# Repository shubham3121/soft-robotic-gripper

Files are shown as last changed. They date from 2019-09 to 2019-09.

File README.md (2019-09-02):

# soft-robotic-gripper

This was my under-graduate final year research project. This project captures the developement of a soft robotic gripper that exhibits the grasping and release action similar to a human hand. The use of NiTi coils as actuators, instead of servo motors, for producing the grasp and release motion, differentiates this robotic gripper from existing ones. This repository consits of:
- source code files for the micro-controller
- Related cad models and gcode files
- Detailed report on the robotic gripper
- A copy of the paper that was submitted to IEEE Transactions on Robotics (RAS Society)
- Link to video of the prototype: https://youtu.be/JxMexBUdsPk

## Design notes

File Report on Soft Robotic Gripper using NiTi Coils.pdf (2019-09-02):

### A Project on

## Soft Robotic Gripper Using NiTi Coils

### Submitted for fulfilment of award of

### Bachelor of Technology

In

### Electrical and Electronics

By

### Raghvendra Singh Shubham Gupta Utkarsh Rastogi

### Under the Guidance of

### Vikash Kumar Rahul Dixit

### AJAY KUMAR GARG ENGINEERING COLLEGE, GHAZIABAD

### YEAR: 2015-2016

AJAY KUMAR GARG ENGINEERING COLLEGE,

### GHAZIABAD

# CERTIFICATE

### This is to certify that Project Report entitled "SOFT ROBOTIC GRIPPER

### USING NiTi COILS” which is submitted by Raghvendra Singh, Shubham

### Gupta and Utkarsh Rastogi in the partial fulfillment of requirement for the

### award of degree of Bachelor of Technology (Electrical and Electronic

### Engineering) submitted to A.P.J Abdul Kalam Technical University, Lucknow

### is a record of students' own work carried out under my supervision. The

### matter in this report has not been submitted to any University or Institution

for award of any degree.

Supervisors:
Vikash Kumar
Rahul Dixit

HOD:
Prof. Ashiv Shah
TIFAC CORE

Date: 29th April, 2016.

ACKNOWLEDGEMENT

We take this opportunity to express our deep sense of gratitude and regard to Mr. Vikash Kumar

(TIFAC CORE Deptt.) and Mr. Rahul Dixit (TIFAC CORE Deptt.), Ajay Kumar Garg

Engineering College, Ghaziabad for his continuous encouragement and able guidance, we needed

to complete this project.

We would pay sincere gratitude to the Head of the Deptt. (TIFAC CORE) Prof. Ashiv Shah for his

precious and enlightening words of wisdom which motivated us throughout our project work.

We are also grateful to Mr. Ashish Gupta and Mr. Harikesh Bahadur Singh for their continuous

support and valuable suggestions.

DECLARATION

### We hereby declare that this submission is our own work and that, to the best

### of out knowledge and belief, it contains no material previously published or

### written by another person, nor material which to a substantial extent has been

### accepted for the award of any other degree or diploma by the university or

### other institute of higher learning, except where due acknowledgement has

been made in the text.

### Signature:

1.

### Name: Shubham Gupta

### Roll No. : 1202721090

2.

### Name: Raghvendra Singh

### Roll No. : 1202721065

3.

### Name: Utkarsh Rastogi

### Roll No. : 1202731109

Chapter 1.

Chapters | | PageNo.
Chapter I:`` Introduction | 1-5
1.1 | Robot End Effectors | 1
1.2 | Biologically Inspired Engineering | 2
| 1.2.1 Bio-inspired Robotics | 2
| 1.2.1.1 Soft Robotics | 3
1.3 | Mechanism of Gripping | 3
| 1.3.1 Shape of the Gripping Surface | 3
| 1.3.2 Force Required to Grip the Object | 3
1.4 | Examples of End Effectors | 4
Chapter II: Literature Review, Requirement Analysis & Feasibility Study | 6-19
2.1 | Literature Review | 6
| 2.1.1 NiTi Coil Actuators as Micro Artificial Muscle Fibers | 7
| 2.1.2 Modelling of NiTi Coil Actuators | 7
| 2.1.3 Fabrication & Characteristics of NiTi Coils | 10
2.2 | Requirement Analysis | 13
| 2.2.1 Initial Proposed Wire & Spring Specifications | 13
| 2.2.1.1 Cost Associated | 14
2.2.2 Designing of Coil Actuators using Standard NiTi Springs 14
| 2.2.2.1 Stretch Ratio | 14
| 2.2.2.2 New Spring Specifications | 15
2.3 | Feasibility Analysis | 16
| 2.3.1 Operational Feasibility | 16
| 2.3.2 Electrical Guidelines | 18
| 2.3.3 Cycle Time | 18
Chapter III: System Analysis, Modelling & Design | 20-29
3.1 | System Analysis | 20
3.2 | Modelling of the Spring Actuators | 21
3.3 | Modelling of the Fingers of the Gripper | 22
| 3.3.1 Designing of the Finger Link | 23
| 3.3.2 Fabrication of the Link | 24
| 3.3.3 Construction of the Finger of the Gripper | 25
| 3.3.4 Designing & Modelling Of Gripper Base | 27
3.4 | Assembling of the Three Finger Gripper | 28
Chapter IV: Hardware & Software Specifications | 30-42
4.1 | Hardware Specifications | 30
| 4.1.1 BC368 NPN General Purpose Amplifier | 30
| 4.1.2 Tiva™ TM4C123GH6PM Microcontroller | 32
| 4.1.2.1 TM4C123GH6PM Microcontroller Overview | 33
| 4.1.2.2 TM4C123GH6PM Microcontroller Pin Structure | 33
| 4.1.2.3 Tiva Launchpad based on TM4C123GH6PM | 35
| 4.1.3 LM2596 DC-DC Step Down Buck Converter | 37

TABLE OF CONTENTS

4.2 | Software Specifications | 38
4.2.1 Code for the Microcontroller | 39
4.3 | Control Circuit for the Gripper | 41
Chapter V: Working of Project | 42-45
5.1 | Analogy between the Human Hand & the Robotic Gripper | 43
5.1.1 Power Grip | 43
5.1.2 Precision Grip | 43
5.2 | Implementation of the Robotic Gripper | 44
Chapter VI: Results & Discussion | 46-47
6.1 | Advantages of Developed System | 46
6.2 | Limitations | 46
Chapter VII: Conclusion & Future Scope | 48
7.1 | Conclusion | 48
7.2 | Future Scope | 48
References

LIST OF FIGURES

Figure 1.1 | Examples of End Effector | 5
Figure 2.1 | Image of a muscle fiber of 400µm diameter and length of 0.5m | 6
Figure 2.2 | Five representational states of a NiTi coil spring actuator in Austenite and Martensite phase with and without load . | 8
Figure 2.3 | Diagram shows a simple manufacturing system that enables the fabrication of long strand coiled springs of NiTi muscle fiber | 10
Figure 2.4. | Experimental results of NiTi coil spring ... | 12
Figure 2.5 | Example of Stretch Ratio | 15
Figure 2.6 | Various basic structures and the percentage of movement of NiTi wire/coils | 17
Figure 3.1 | Bones of the left hand (Volar Surface) | 20
Figure 3.2 | Front, Top and left view of the finger link | 23
Figure 3.3 | Ultimaker2 and the spool of used as the printing filament | 25
Figure 3.4 | Representation of the various components in the link model | 26
Figure 3.5 | Front, Left and Isometric view of the assembly of finger links | 26
Figure 3.6 | Top, Left and Front view of the model of the gripper | 28
Figure 3.7 | Snapshots of the three fingers of the gripper and a completely assembled gripper | 29
Figure 4.1 | Pin configuration of BC368 NPN General Purpose Amplifier | 31
Figure 4.2 | Table showing the features of TM4C123GH6PM Microcontroller | 33
Figure 4.3 | I/O port pins for the TM4C123GH6PM Microcontroller | 34
Figure 4.4 | Tiva LaunchPad based on the TM4C123GH6PM | 35
Figure 4.5 | Switch and LED interfaces on the Tiva LaunchPad Evaluation Board | 36
Figure 4.6 | Interface connectors on the Tiva TM4C123 LaunchPad Evaluation Board | 36
Figure 4.7 | LM2596 DC-DC Step down Buck Converter and its circuit diagram | 37
Figure 4.8 | Control circuit for the robotic gripper | 41
Figure 5.1 | Control circuit during grasp action and release action of the gripper | 45
Figure 6.1 | Gripper during gripping of an object | 46

ABSTRACT

Robotics is basically based on the fundamental assumption that robots are chain of rigid links but ‘Soft Robotics’ which is the use of soft materials in robotics that can vary their stiffness and thus can undergo high deformations during interactions that overcomes robot’s basic assumptions and thus removes many bottlenecks of rigid links in robots. They can have mechanisms for varying the material characteristics such as stiffness, elasticity and surface properties, etc. for generating motion through muscles and for facilitating sensing in skins through embedded mechanoreceptors. Soft materials may enable us to automate tasks that are beyond capacities of current robotics technology and thus the complex, precise control architecture can be simplified using highly compliant materials with variable stiffness. Soft Robots has the expected capability to interact more
easily and effectively with the real world environment. | Soft Robotics has the potential to
produce a new generation of better robots.
This report presents the development and analysis of a soft robotic platform that exhibits the grasping and release action of a human hand. The design of the gripper is basically based on a human hand except for the fact that all the joint to joint distances in a finger are equal. Each finger is composed of four sub-components and three fingers are joint together to a base to form the hand. Nickel titanium (NiTi) coils are used as the actuating medium and are placed across the joints of the finger. The finger sub-components are made of PLA using a 3D printer. The actuation of the nickel titanium coils is controlled through a constant current supply, controlled through a switching circuit and a microcontroller. This approach allows for a simple, low cost, energy efficient gripper. The report further analysis and discusses the potential use and application of this platform.

Index Terms—Robotic gripper, nickel titanium (NiTi) coil actuators, PLA, soft robotics, shape memory alloys (SMA) actuation, microcontroller, 3D printer.

Chapter 1.
INTRODUCTION
1.1 | Robot End Effectors
| In robotics, an end effector is the device at the end of a robotic arm, designed to
interact with the environment. The exact nature of this device depends on the application of the robot. In the strict definition, which originates from serial robotic manipulators, the end effector means the last link (or end) of the robot. At this endpoint the tools are attached. In a wider sense, an end effector can be seen as the part of a robot that interacts with the work environment. This does not refer to the wheels of a mobile robot or the feet of a humanoid robot which are also not end effectors—they are part of the robot's mobility.
| End effectors may consist of a gripper or a tool. When referring to robotic prehension
there are four general categories of robot grippers, these are: [1]
a) Impactive – jaws or claws which physically grasp by direct impact upon the object.
b) Ingressive – pins, needles or hackles which physically penetrate the surface of the
| object (used in textile, carbon and glass fibre handling).
c) Astrictive – suction forces applied to the objects surface (whether by vacuum,
| magneto or electro adhesion).
d) Contigutive – requiring direct contact for adhesion to take place (such as glue,
| surface tension or freezing). They are based on different physical effects used to guarantee a stable grasping

between a gripper and the object to be grasped.[2] Industrial grippers can be mechanical, the most diffused in industry, but also based on suction or on the magnetic force. Vacuum cups and electromagnets dominate the automotive field and in particular metal sheet handling. Bernoulli grippers exploit the airflow between the gripper and the part that causes a lifting force which brings the gripper and part close each other (i.e. the Bernoulli's principle). Bernoulli grippers are a type of contactless grippers, namely the object remains confined in the force field generated by the gripper without coming into direct contact with it. Bernoulli grippers have been adopted in photovoltaic cell handling, silicon wafer handling, and also in the textile and leather industries. Other principles are less used at the macro scale (part size >5mm), but in the last ten years they demonstrated interesting applications in micro handling. Some of them are ready of spreading out their original field. The other adopted principles are: Electrostatic grippers and van der Waals grippers based on electrostatic charges (i.e. van der Waals' force), capillary grippers and cryogenic grippers, based on liquid medium, and ultrasonic grippers and laser grippers, two contactless grasping principles. Electrostatic grippers are based on charge difference between the gripper and the part (i.e. electrostatic force) often activated by the gripper itself, while van der Waals grippers are based on the low force (still electrostatic) due to the atomic attraction between the molecules of the gripper and those of the object.
| Capillary grippers use the surface tension of a liquid meniscus between the gripper
and the part to center, align and grasp the part, cryogenic grippers freeze a small amount of liquid and the resulting ice guarantees the necessary force to lift and handle the object (this principle is used also in food handling and in textile grasping). Even more complex are ultrasonic based grippers, where pressure standing waves are used to lift up a part and trap it at a certain level (example of levitation are both at the micro level, in screw and gasket handling, and at the macro scale, in solar cell or silicon wafer handling), and laser source that produces a pressure able to trap and move micro parts in a liquid medium (mainly cells). The laser gripper are known also as laser tweezers.
A particular category of friction/jaw gripper are the needle grippers: they are called intrusive grippers and exploits both friction and form closure as standard mechanical grippers. The most known grippers can be of two, three or even five fingers. The end effectors that can be used as tools serve various purposes, such as spot welding in an assembly, spray painting where uniformity of painting is necessary, and for other purposes where the working conditions are dangerous for human beings. Surgical robots have end effectors that are specifically manufactured for the purpose.

1.2 Biologically Inspired Engineering

[3] Biologically inspired engineering is a new scientific discipline that applies biological principles to develop new engineering solutions for medicine, industry, the environment, and many other fields that have previously not been touched by the biology revolution. The emergence of this new discipline is the culmination of the unification of the life sciences with engineering and the physical sciences, and it is leading to an ever deeper understanding of how life works. Biologically inspired engineering involves deep exploration into the way that living cells, tissues, and organisms build, control, manufacture, recycle, and adapt to their environment. Bioinspired engineers leverage this knowledge to innovate new technologies and translate them into products that meet real world challenges.
| Biologically inspired engineering is an interdisciplinary field encompassing many
specialty areas in biology (molecular cell biology, genetic engineering, developmental biology, organismal biology, clinical medicine), engineering (biomedical engineering, chemical engineering, mechanical engineering, electrical engineering, robotics), and the physical sciences (chemistry, physics, materials science, and nanotechnology). Integrated research programs in this area span many of these disciplines and include biomimicry, as well as analysis of the way that living systems form and function using self-assembling nanomaterials, complex dynamic networks, nonlinear dynamical control, self-organizing behaviour, evolution, and natural selection.

1.2.1 Bio-inspired Robotics

| Bio-inspired robotic locomotion is a fairly new sub-category of bio-inspired
design. It is about learning concepts from nature and applying them to the design of real world engineered systems. More specifically, this field is about making robots that are inspired by biological systems. Biomimicry and bio-inspired design are sometimes confused. Biomimicry is copying the nature while bio-inspired design is learning from nature and making a mechanism that is simpler and more effective than the system observed in nature. Biomimicry has led to the development of a different branch of robotics called soft robotics. The biological systems have been optimized for specific tasks according to their habitat. However, they are multi-functional and are not designed for only one specific functionality.
| Bio-inspired robotics is about studying biological systems, and look for the
mechanisms that may solve a problem in the engineering field. The designer should then try to simplify and enhance that mechanism for the specific task of interest. Bio-inspired roboticists are usually interested in biosensors (e.g. eye), bio actuators (e.g. muscle), or biomaterials (e.g. spider silk). Most of the robots have some type of locomotion system. Thus, in this article different modes of animal locomotion and few examples of the corresponding bio-inspired robots are introduced.

1.2.1.1 Soft Robotics

Soft robotics (https://en.wikipedia.org/w/index.php?title=Soft_robotics&action=edit&redlink=1) [4] is a new field in robotics and the idea is to make all of the components in the robot soft and flexible in order to move in very limited spaces and change gaits fairly easily. This field is inspired by animals such as octopus (https://en.wikipedia.org/wiki/Octopus) or starfish. (https://en.wikipedia.org/wiki/Starfish) One of the first multigait soft robots is developed at Harvard University and is inspired by
starfish. | [5] | Soft robotics is not just a new direction of technological development, but a
novel approach to robotics, unhinging its fundamentals, with the potential to produce a new generation of robots, in the support of humans in our natural environments.
1.3 | Mechanism of Gripping
| A common form of robotic grasping is force closure. [6] Generally, the gripping
mechanism is done by the grippers or mechanical fingers. Generally only two finger grippers are used for industrial robots as they tend to be built for specific tasks and can therefore be less complex.
The fingers are also replaceable whether or not the gripper itself is replaced. There are two mechanisms of gripping the object in between the fingers (for the sake of simplicity, the following explanations consider only two finger grippers).

1.3.1 Shape of the gripping surface

| The shape of the gripping surface of the fingers can be chosen according to the
shape of the objects that are to be manipulated. For example, if a robot is designed to lift a round object, the gripper surface shape can be a concave impression of it to make the grip efficient, or for a square shape the surface can be a plane.

1.3.2 Force required to grip the object

| Though there are numerous forces acting over the body that has been lifted by the
robotic arm, the main force acting there is the frictional force. The gripping surface can be made of a soft material with high coefficient of friction so that the surface of the object is not damaged. The robotic gripper must withstand not only the weight of the object but also acceleration and the motion that is caused due to frequent movement of the object. To find out the force required to grip the object, the following formula is used:

F = µWn
| Where: F is the force required to grip the object, µ is the coefficient of friction, n is the number of fingers in the gripper and W is the weight of the object.

But the above equation is incomplete. The direction of the movement also plays an important role over the gripping of the object. For example, when the body is moved upwards, against the gravitational force, the force required will be more than towards the gravitational force. Hence, another term is introduced and the formula becomes:

F = µWng

Here, the value of g should not be taken as the acceleration due to gravity. In fact, here g stands for multiplication factor. The value of g ranges from 1 to 3. When the body is moved in the horizontal direction then the value is taken to be 2, when moved against the gravitational force then 3 and along the gravitational force, i.e., downwards, 1.

1.4 | Examples of End effectors
| The end effector of an assembly line robot would typically be a welding head, or a
paint spray gun. A surgical robot's end effector could be a scalpel or others tools used in surgery. Other possible end effectors are machine tools, like a drill or milling cutters. The end effector on the space shuttle’s robotic arm uses a pattern of wires which close like the aperture of a camera around a handle or other grasping point.
(a.) | (b.)
(c.) | (d.)

(e)

Fig. 1.1 (a.) An example of a basic force-closure end effector. (b.) A spot welding end effector. (c.) A repair and observation end effector in use in space (Canadarm2). (d.) A highly sophisticated attempt at reproducing the human-hand force-closure end effector. (e.) Laser Welding end effector.

Chapter 2.
LITERATURE REVIEW, REQUIREMENT ANALYSIS & FEASIBILITY

2.1 Literature Review

[7] Soft robotics is an emerging field that introduces a number of new challenges to roboticists. Soft robots will consist of a flexible body, possess an ability to deform their shape as dictated by various environments, and exhibit superb robustness upon impacts. One of the most challenging elements of such a robot is the soft actuator. Most conventional actuators contain rigid components that limit morphing ability, however a soft actuator can deform along with the surrounding structure.
| One of these soft actuators is Nickel Titanium (NiTi) a Shape Memory Alloy (SMA),
since its unique martensite transformation makes it inherently flexible. It is also well known for its high energy density, despite its poor efficiency. NiTi has great advantages especially in a small scale where other types of actuators are not available or exhibit poor energy density. The NiTi crystal lattice transforms from the martensite state to the austenite state and produces up to 4% length change as it is heated through the transition temperature range. Some applications require more operating strain to satisfy the dimensional constraints. In order to create larger stroke lengths out of a small lattice structure alteration, NiTi can be restructured into coil springs.

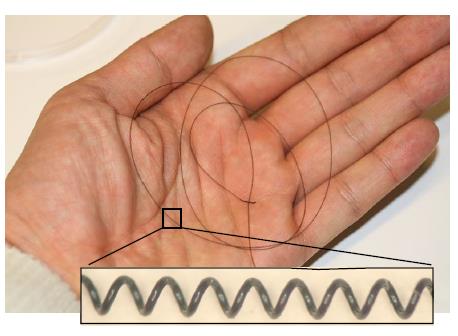
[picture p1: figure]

Fig. 2.1 Fabricated muscle fiber is 400µm in diameter and 0.5m

Chang et al. [8], discuss the numerous models for NiTi that has been proposed since the early 1990s. Most of them are thermodynamic models of NiTi wires, tubes, and sheets. Some papers discuss NiTi springs [9], [10], [11], [12], [13], but the models used in these papers are not complete. The paper [7], presents a more complete model that can be used as a design guideline for NiTi spring actuators.

NiTi coil springs are created from straight wire wound into a coil shape and annealed at a high temperature to reset the ‘memorized’ shape. The annealing temperature used in the reshaping process affects mechanical properties of NiTi and actuation performance. The results from experiments to show the variation in properties due to the variation in annealing temperature have also been presented. These experiments include detwinning force and loaded displacement measurements. After weightlifting test, springs shows permanent deformation, which is also function of the annealing temperature.

2.1.1 NiTi Coil Actuators as Micro Artificial Muscle Fibers

NiTi is one of the well-known SMA materials that generate mechanical work by phase change. Despite its low efficiency, it has a high energy density, which gives the ability to develop relatively small scale actuators compared to other types of actuators mentioned in Section I. In a solid state phase transformation, the crystal structure of the NiTi compound transforms from martensite to austenite states with up to 7% strain change [14]. For larger displacements, coiled spring NiTi wires can be used.
Various NiTi models suggested from the 1990s are discussed in [15]. These are mostly thermodynamic models of various forms of NiTi such as wires, tubes, and sheets. Coiled spring NiTi models were discussed in [9], and [10]–[12]. These models, however, are relatively incomplete. The existing models focus on the mechanical coiled spring equations using different shear moduli for the martensite and austenite phases, overlooking the change in the free length of the spring due to the phase transition.
A more appropriate model, which is useful for a design of coiled spring NiTi is proposed in Section 2.1.2. This model combines the mechanical and thermodynamic aspects of NiTi coil actuators to describe the overall martensite deformation and the geometrical spring effect together. We use this model as a guideline for actuator design for the Meshworm robot.
There are two major steps to fabricate NiTi coil springs. First, a NiTi wire is wound around a straight core, and then the coiled NiTi wire is annealed at a certain high temperature in order to reset the memorized shape as a spring. During the annealing process, mechanical properties and the actuation performance of NiTi springs are determined by the annealing temperature. In Chapter 2.1.2, the manufacturing process is detailed and experimental data between deflection and force under various annealing temperatures are presented.

2.1.2 Modelling of NiTi Coil Actuators

Even though NiTi spring actuators are widely used [9], [10]–[12], complete design models have not been developed yet. Recent works utilize the mechanical coiled spring equation with two shear moduli, GMand GA which are the martensite and austenite phases, respectively. However, none of these models consider the free length change of the NiTi spring due to phase change. The free length of 100% austenite phase xAo is shorter than the free length of 100% martensite xMo.
There are two major physical phenomena in NiTi coil spring deformation. One is the free length change due to the phase transformation explained earlier, and the other is the spring constant difference between the martensite and austenite states. The spring constant in the austenite phase is around 2–3 times greater than in the martensite phase [15].

[16] Fig. 2.2 shows five typical states of a NiTi coil spring during actuation. When the NiTi coil is heated up above the phase transition temperature, it becomes austenite and fully contracts as in Fig. 2.2(a). If a load F is applied in this state, the spring will have a displacement δH as shown in Fig. 2.2(b). When the temperature is below the transition temperature, it becomes martensite and the crystal structure of NiTi twins [17] without an observable overall shape change [see Fig. 2.2(c)]. If a load is applied below the transition temperature, the crystal structure is detwinned [17]. Fig. 2.2(e) shows the detwinned martensite with a load F, and Fig. 2.2(d) shows the detwinned martensite in free length after the detwinning load is removed. The free length difference between austenite and detwinned martensite is δM. The displacement δL
is the length difference between loaded martensite and unloaded martensite under fully detwinned status.
In general, the NiTi spring actuation cycle starts in the martensite phase with an external load F. And then, the spring is activated by heating it up to transition temperature, which results in a spring length contraction under the load. The displacement created in this transformation is called effective displacement,δeffective and calculated as follows:
δeffective = δM + δL − δH | (1)

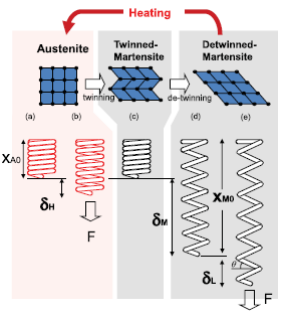
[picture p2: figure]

Fig. 2.2. Five representational states of a NiTi coil spring actuator: (a) full austenite without load (b) full austenite with load, (c) twinned martensite without load, (d) fully detwinned martensite without load, and (e) fully detwinned martensite with load.

Here, each δi value, where i ∈ {H, L, M}, corresponds to the displacement of the coil. Using the general coiled spring deflection equation, δi
is a function of an external load F, overall spring diameter D, NiTi wire diameter d, number of active coils in the spring n, and the shear modulus of the spring after annealing G

δi =

8FD

3n
Gd⁴

(2)

The shear strain γ of the spring is

γ =

τ
G

(3)

and the shear stress τ is

τ =

8FDҡ
πd³

(4)

where ҡ is a stress correction factor. From Wahl’s formula [18],

ҡ =

4C−1
4C−4

+

0.615
C
. | (5)

Here C is the spring index, defined as follows:

C =

D
d
. | (6)

Using this analysis, the difference of the free length between the austenite and martensite phases δM can be calculated from (2) through (4) as

δM =

πγD

2n

dҡ

. | (7)

Therefore, for a given F, the effective displacement from (1) is given as follows:

δeffective =

πγD

2n

dҡ

+

8FDeff

3 n
GMd⁴ −

8FD

3n
GAd⁴
. | (8)

There is a significant coil diameter D change when the coil spring is elongated under martensite phase with a load F. Therefore, to calculate the displacement properly in this situation, an effective spring diameter Deff is used

Deff = D cos θ

where θ is the angle between the spring wire and the horizontal plane.

2.1.3 Fabrication and Characterization of NiTi Coil Actuators

[16] The fabrication process of micro-NiTi coil muscle fibers is depicted schematically in Fig. 2.3. One end of a 200-μm diameter core wire and a 100-μm diameter NiTi wire [Dynalloy Flexinol (R)] are clamped at a drill press. Constant tension is applied to the core wire by attaching a weight on the free end. A metal tube and a bar attached to the tube make up the coil guide, which is essential for closely packing the NiTi coil on the core. The friction of the metal tube on the core acts against the tension from the coiled NiTi and keeps the core wire vertical.

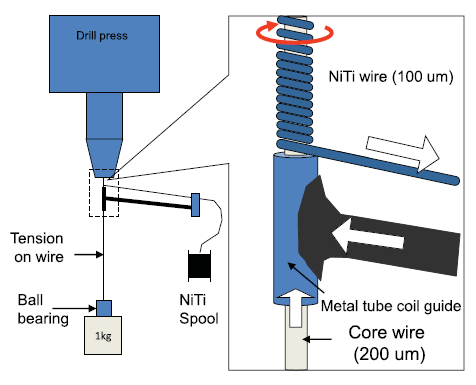
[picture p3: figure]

Fig. 2.3. Simple manufacturing system enables the fabrication of long strand coiled springs of NiTi muscle fiber. The core wire is under tension and a NiTi wire is wound around the core. The guidance tube is slightly larger than the core wire. The tension of the NiTi wire is maintained by friction between NiTi and the long bar.

After winding the NiTi wire to a given length, the ends of the coil are clamped to the core wire and annealed in an oven under a controlled temperature. The annealing temperature determines various parameters of the resulting spring actuator. Two noticeable trends are identified that vary with the annealing temperature: 1) increasing the annealing temperature decreases the detwinning force, and 2) large annealing temperatures cause the resulting springs to lose their ability to return to their original dimensions after loading. Detwinning is a passive process that returns the actuated NiTi coils in the twinned martensite state back to the fully detwinned martensite state through martensite transformation. This requires external work, such that a certain amount of tensile force pulls the coils to extend them, transforming their state in the process. This force is strongly dependant on the annealing temperature, and is a mechanical characteristic of the actuators. When used in an antagonistic configuration, such that the actuation of one coil detwins the other, this characteristic force requirement affects the full cycle work efficiency of the actuators.
We experimentally investigated the dependence of the detwinning force on the annealing temperature. 25-mm-long NiTi coil springs are annealed at nine different temperatures ranging from 300 ◦C to 540 ◦C in 30 ◦C increments. Weights are hanged on the coils to apply varying external forces. Weight application and removal were carried out slowly to reduce dynamic effects and the spring effect. The final elongated length was measured under no load, after the weights were removed.
Fig. 2.4(a) depicts the results. In these curves, detwinning is indicated as a plateau, similar to a plastic deformation behaviour in stress–strain curves. The value at which this plateau occurs is the detwinning force. This force clearly decreases with the increasing annealing temperature as a general trend. After detwinning, the coils yield a larger stiffness, indicated by a sharp gradient in the curve after the plateau. This stiffness change occurs at larger deflections as the annealing temperature is increased. We used an annealing period of 20 min for these experiments. We found no change in actuator characteristics above this value.

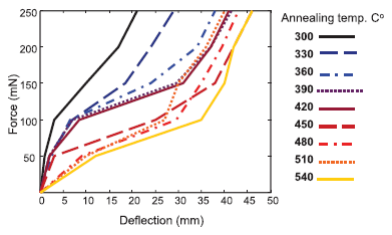
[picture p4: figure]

(a)

(b)

(c)

Fig. 2.4. Experimental results of NiTi coil spring. (a) Deflection of springs annealed at various temperatures under load. (b) Permanent plastic deformation of NiTi coil springs annealed at various temperatures, after lifting a 35-g weight. (c) Experimental NiTi coil spring deflection data are compared to the theoretical model predictions: Average errors in Martensite and Austenite phases’ are−22% and 12.4%, respectively.

The second effect of the annealing temperature on the NiTi coil actuator operation is shown in Fig. 2.4(b). This is a curve of permanent deformation of these actuators, 25 mm in original length, after lifting a 35-g weight only once. The permanent deformation is measured as the difference between the final length in the austenite state after lifting and the original length of the coils. The data indicate that springs annealed at a temperature below 400 ◦C show reasonable consistency at multiple trials. In contrast, springs annealed at higher temperatures yield large permanent deformations after multiple trials. In short, even though higher annealing temperatures result in smaller detwinning forces, the original dimension is lost for springs annealed above 400 ◦C after a single lifting cycle, a trade off in fabrication. Based upon these observations, we used a NiTi coil spring annealed at 390 ◦C for further experiments. Weight lifting experiments are performed and stroke lengths are measured for comparison of the model output with experimental results. Fig. 2.4(c) displays our results of deflection of springs in both the austenite and the martensite states with various loads. We applied a constant current of 150 mA to maintain the spring in the austenite state under load. Model predictions from (2) are plotted with the experimental data. The shear modulus of NiTi is also a function of the annealing temperature. Thus, we calculated this value through the deflection length in the austenite state. As the martensite state shear modulus, we used a third of the austenite shear modulus, which is the typical case for NiTi [18].
The work done by the NiTi coil springs when they lift a known weight yields the energy density of these actuators. A 25 mm long NiTi coil annealed at 390 ◦C lifts a 37.9-g weight with a stroke length of 50 mm. The total energy to perform this task is then 0.0184
J. The weight of the NiTi coil is 0.014 g. Thus, the energy density, defined as the amount of work done by unit mass of this actuator in a single stroke, is calculated to be 1314 J/kg.

2.2 | Requirement Analysis
| The main and the foremost most import requirement for this project are the NiTi
coils. Modelling of these springs are the most important as they serve as the actuators in the gripper. Initially, manufacturing of customised springs based on the equation (8), discussed in section 2.1.2, was proposed.

2.2.1 Initial Proposed Wire and Spring Specifications

The table below specifies the initial proposed wire (NiTi) specifications, used to manufacture the NiTi springs.

Diameter Size (Inches) | Resistance (Ohms/ Inch) | Maximum Pull Force (grams) | Approximate Current at Room Temperature (mA) | Contraction Time (seconds) | Off Time LT=70°C Wire (seconds)
0.004 | 8.0 | 150 | 180 | 1 | 0.8

The following wire specification was selected due to its low resistance, low contraction time and low off time. Lower the contraction time and off time, faster would be the actuation of the springs.

Initially customised springs were proposed which were of different lengths. This was because the NiTi coils were to be attached between the joints of the fingers. But, since the length between the joints of a human finger is different hence four springs of different solid lengths for a single finger was proposed. Since we required an approximate displacement of 5mm by the NiTi coils during its actuation, hence the length of the coil in various phases (martensite and austenite) were calculated according to the equation (8) given in section 2.1.2.

The table below gives the specification of NiTi coils for the back side and palm side of the hand.

Back Side
| Spring 1 | Spring 2
Spring Diameter | 285µm | 285µm
Solid Length | 20mm | 17.5mm
End Conditions | Hooks | Hooks
Cold-Loaded Length | 26.7116 mm | 24.2119 mm
Hot Loaded Length | 21.812 mm | 19.312 mm
Clearance | 0.158202 mm | 0.0009179 mm
Number of Turns | 167.76 | 167.76

Palm Side
| Spring 1 | Spring 2
Spring Diameter | 350µm | 350µm
Solid Length | 15mm | 10mm
End Conditions | Hooks | Hooks
Cold-Loaded Length | 21.712 mm | 16.712 mm
Hot Loaded Length | 16.812 mm | 11.812 mm
Clearance | 0.05787 mm | 0.0026716 mm
Number of Turns | 90.58 | 90.58

2.2.1.1 Cost Associated

DYNALLOY, Inc. (a company dedicated to providing products related to Dynamic Alloys) offered to help us and provide customise springs made up of NiTi, sold with the name of Flexinol. We required about 5-6 each type of springs, so we require around 20 springs altogether. A technical associate at the company studied our specifications and estimated the overall cost of production of customised NiTi coils to be around $10000. This was a high cost to be accustomed to as we wanted our product to be cheap and affordable. Hence we shifted to the use of standard springs which was provided by the company. This helped us in decreasing the overall cost of the springs by almost 80 percent. But in order to make use of standard Flexinol springs, we needed some changes in our design.

2.2.2 Designing of the Coil Actuators using Standard NiTi Springs

[19] DYNALLOY, Inc. provides NiTi products under the trade name of Flexinol®. Flexinol® Actuator Wires are small diameter wires which contract like muscles when electrically driven. Smaller than motors or solenoids, cheaper and generally easier to use, these wires perform physical movement across an extremely wide variety of applications. Flexinol® is a trade name for shape memory alloy actuator wires. Made of nickel-titanium these small diameter wires contract like muscles when electrically driven. This ability to flex or shorten is characteristic of certain alloys that dynamically change their internal structure at certain temperatures. The idea of reaching higher temperatures electrically came with the light bulb, but instead of producing light these alloys contract by several percent of their length when heated and can then be easily stretched out again as they cool back to room temperature. Like a light bulb both heating and cooling can occur quite quickly. The contraction of Flexinol® actuator wires when heated is opposite to ordinary thermal expansion, is larger by a hundredfold, and exerts tremendous force for its small size. The main point is that movement occurs through an internal "solid state" restructuring in the material that is silent, smooth, and powerful.

2.2.2.1 Stretch Ratio

Flexinol® actuator springs can be an alternative to straight Flexinol® actuator wires for applications with low force and high travel requirements. These springs can contract and relax multiples of their length. When Flexinol® actuator springs are used within the correct range then obtaining repeatable motion from the springs for millions of cycles is reasonable.
[19] Stretch Ratio “SR” is defined as any length “L" over the solid length “SL", in any state, hot or cold. For example a spring with a SR of 4 cold and 2 hot, assuming a solid length “SL” of 10mm would then be 20mm hot, and 40mm cold.

SR = L/SL

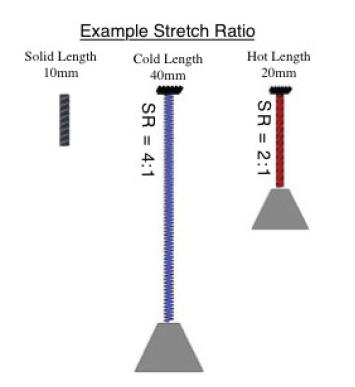
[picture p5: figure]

Fig. 2.5. Represents an example of Stretch Ratio.

2.2.2.2 New Spring Specifications

The following are the specifications of the Flexinol® springs used in the robotic gripper. The specifications also give us a rough idea as to how much current and force to expect with spring of given diameter. The data has been taken from the technical datasheet provided by Dynalloy, Inc.

Spring Wire Diameter: 0.203mm

Outer Diameter: 1.37mm

SR Cold, SR Hot: 14, 5

Displacement/ Coil: 1.8mm

Resistance on Straight Wire: 29.13ohms/meter

*Heating Pull Force: 39.3grams

*Cooling Deformation Force: 15.94grams

Approximate Current for 2 Seconds Contraction: 0.7A

**Cooling Time 90°C “HT” Wire: 3.0 sec

We can calculate the number of turns of the spring using the following formula:

Number of coils ∗ Wire diameter = Solid Lengtℎ

Dynalloy, Inc. provides standard springs with three different wire diameters. The springs with the above described wire diameter (0.203mm) is best suited, as it fulfils the pull force required by the gripper to perform the grasp and release action. Secondly, the spring has the minimum cooling time of the three available springs.

*The Heating pull force is based on ~ 25,000 psi, which for many applications is maximum safe stress for the wire. The cooling deformation force is based on ~ 10,000 psi, which is a good starting point in the design.

The contraction time is directly related to current input. The figures used here are only approximate since room temperatures, air current and heat sinking of specific devices vary.

*Approximate cooling time is at room in static air, using a vertical spring. The last 0.5% of deformation is not used in these approximations. “HT” = High Temperature Flexinol® Actuator Spring.

2.3 Feasibility Analysis

2.3.1 Operational Feasibility

| The movement or stroke of Flexinol® actuator wire is measured as a percentage of
the length of the wire being used and is determined, in part, by the level of stress one uses to reset the wire, or to stretch it in its low temperature phase. This opposing force, used to stretch the wire, is called the bias force. In most applications, the bias force is exerted on the wire constantly, and on each cycle as the wire cools, this force elongates it. If no force is exerted as the wire cools, very little deformation or stretch occurs in the cool, room temperature state and correspondingly very little contraction occurs upon heating. Up to a point the higher the load the higher the stroke. The strength of the wire, its pulling force and the bias force needed to stretch the wire back out are a function of the wire size or cross sectional area and can be measured in pounds per square inch or “psi”. [19] If a load of 5,000 psi (34.5 MPa) is maintained during cooling, then about 3% memory strain will be obtained. At 10,000 psi (69 MPa), about 4% results, and with 15,000 psi (103 MPa) and above, nearly 5% is obtained. However, there is a limit to how much stress can be applied.
| Far more important to stroke is how the wire is physically attached and made to
operate. Dynamics in applied stress and leverage also vary how much the actuator wires move. While normal bias springs that increase their force as the Flexinol® actuators contract have only 3-4% stroke, reverse bias forces which decrease as the actuator wires contract can readily allow the wire to flex up to 7%. Mechanics of the device in which it is used can convert this small stroke into movements over 100% of the wires' length and

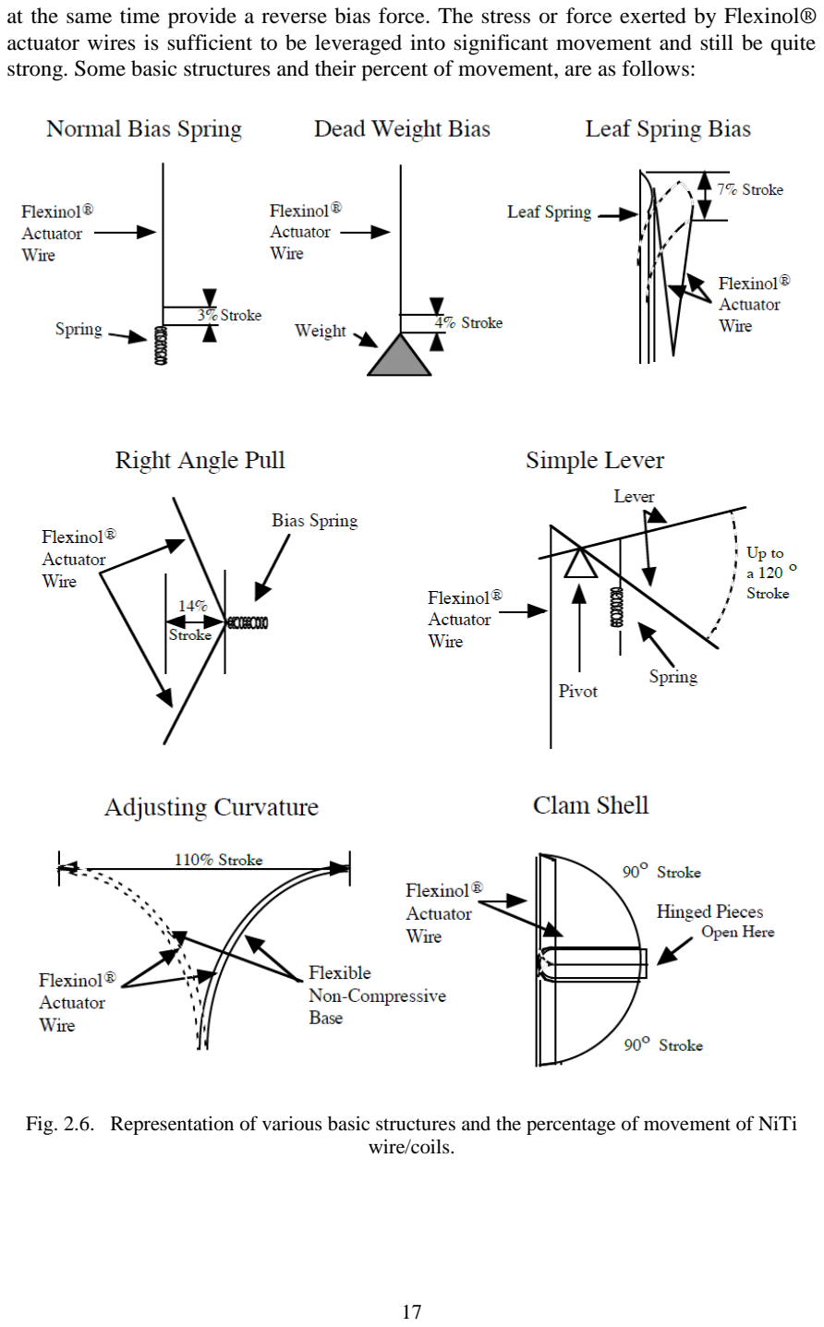
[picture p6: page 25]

at the same time provide a reverse bias force. The stress or force exerted by Flexinol® actuator wires is sufficient to be leveraged into significant movement and still be quite strong. Some basic structures and their percent of movement, are as follows:

Fig. 2.6. Representation of various basic structures and the percentage of movement of NiTi wire/coils.

2.3.2 Electrical Guidelines

[19] If Flexinol® actuator wire is used in the appropriate conditions, then obtaining repeatable motion from the wire for tens of millions of cycles is reasonable. If higher stresses or strains are imposed, then the memory strain is likely to slowly decrease and good motion may be obtained for only hundreds or a few thousands of cycles. The permanent deformation that occurs in the wire during cycling is heavily a function of the stress imposed and the temperature under which the actuator wire is operating. Flexinol® wire has been specially processed to minimize this straining, but if the stress is too great or the temperature too high, some permanent strain will occur. Since temperature is directly related to current density passing through the wire, care should be taken to heat, but not overheat, the actuator wire. The following charts give rough guidelines as to how much current and force to expect with the wire, with diameter of 0.203mm (as stated in section
2.2.2.2) used in the manufacturing of our springs.
Diameter Size (mm) | Resistance (Ohms/ meter) | Pull Force (grams) | Cooling Deformation Force* (grams) | Approximate** Current for 1 Second Contraction (mA) | Cooling Time 194°F, 90°C “HT” Wire (seconds)
0.203 | 29 | 570 | 228 | 660 | 1

* The Heating pull force is based on 25,000 psi (172 MPa), which for many applications is the maximum safe stress for the wire. However, many applications use higher and lower stress levels. This depends on the specific conditions of a given design. The cooling deformation force is based on 10,000 psi (70 MPa), which is a good starting point in a design. Nonetheless, this value can also vary depending on how the material is used.
** The contraction time is directly related to current input. The figures used here are only approximate since room temperatures, air currents, and heat sinking of specific devices vary. On small diameter wires (<= 0.006" diameter) currents that heat the wire in 1 second can typically be left on without over-heating it.
*** Approximate cooling time, at room temperature in static air, using a vertical wire. The last 0.5% of deformation is not used in these approximations.

2.3.3 Cycle Time

The contraction of the Flexinol® actuator wire is due solely to heating and the relaxation solely to cooling. Both contraction and relaxation are virtually instantaneous with the temperature of the wire. As a result mechanical cycle speed is dependent on and directly related to temperature changes. Applying high currents for short periods of time can quickly heat the wire. It can be heated so fast in fact that the limiting factor is not the rate at which heating can occur but rather the stress created by such rapid movement. If the wire is made to contract too fast with a load, the inertia of the load can cause over stress to the wire. To perform high speed contractions inertia must be held low and the current applied in short high bursts. Naturally, current which will heat the wire from room temperature to over 212 °F (100°C) in 1 millisecond, will also heat it much hotter if left on for any length of time [19].
While each device has quite different heat sinking and heating requirements, a simple rule of thumb test can be used to prevent overheating. Measuring the actual internal temperature of the wire across such short time periods is somewhat problematic, however, one can tell if the actuator wire is overheated simply by observing if the wire immediately begins to cool and relax when the current is shut off or not.
If it does not begin to relax and elongate under a small load promptly, when the power is cut, then the wire has been needlessly overheated and could easily be damaged. Simple visual observation is all that is needed to design measured heating circuitry.
Flexinol® actuator wire has a high resistance compared to copper and other conductive materials but is still conductive enough to carry current easily. In fact one can immerse the wire in regular tap water and enough current will readily flow through it to heat it. All of the conventional rules for electrical heating apply to the wire, except that its resistance goes down as it is heated through its transformation temperature and contracts. This is contrary to the general rule of increased resistance with increased temperature. Part of this drop in resistance is due to the shortened wire, and part is due to the fact that the wire gets thicker as it shortens, roughly maintaining its same three-dimensional volume. It makes no difference to the wire whether alternating current, direct current, or pulse width modulated current is used.
Again relaxation time is the same as cooling time. Cooling is greatly affected by heat sinking and design features. The simplest way to improve the speed of cooling is to use smaller diameter wire. The smaller the diameter the more surface to mass the wire has and the faster it can cool. Additional wire, even multiple strands in parallel, can be used in order to exert whatever force is needed. The next factor in improving the relaxation or cooling time is to use higher temperature wire. This wire contracts and relaxes at higher temperatures. Accordingly the temperature differential between ambient or room temperature and the wire temperature is greater and correspondingly the wire will drop below the transition temperature faster in response to the faster rate of heat loss.
Other methods of improved cooling are to use: forced air, heat sinks, increased stress (this raises the transition temperature and effectively makes the alloy into a higher transition temperature wire), and liquid coolants. Combinations of these methods are also effective. Relaxation time can range from several minutes (i.e. delay switches) to fractions of milliseconds (i.e. miniature high speed pumps) by effective and proper heat sinking. Better cooling methods are likely to require more current or heat to move and/or hold the wire in an "on" position. In some cases one may wish to quickly turn the wire on (that is electrically heat it until it contracts) then hold it on for some time. This will likely require a two-step driving current with a larger current to heat the wire and a reduced current to keep it hot without overheating it. There are a number of simple circuits, which will do this.

Chapter 3.
SYSTEM ANALYSIS, MODELLING AND DESIGN
3.1 | System Analysis
| The robotic gripper is inspired by the structure and movement of the human hand.
Hence in order to model a gripper based on the anatomy of the hand, a basic study of the structure of the hand that aid in its movement is necessary.[20] The muscles in the forearm and palm (thenar muscles) all work together to keep the wrist and hand moving, stable, and aligned. The image below shows the bones from the back side of the hand. The red lines show where the tendons attach the muscles to the bones.
| The muscles that move the fingers and thumb are above the wrist in the forearm.
Long flexor tendons extend from the forearm muscles through the wrist and attach to the small bones of the fingers and thumb. When you bend or straighten your finger, these flexor tendon slide through a snug tunnel, called the tendon sheath that keeps the tendon in place next to the bones.

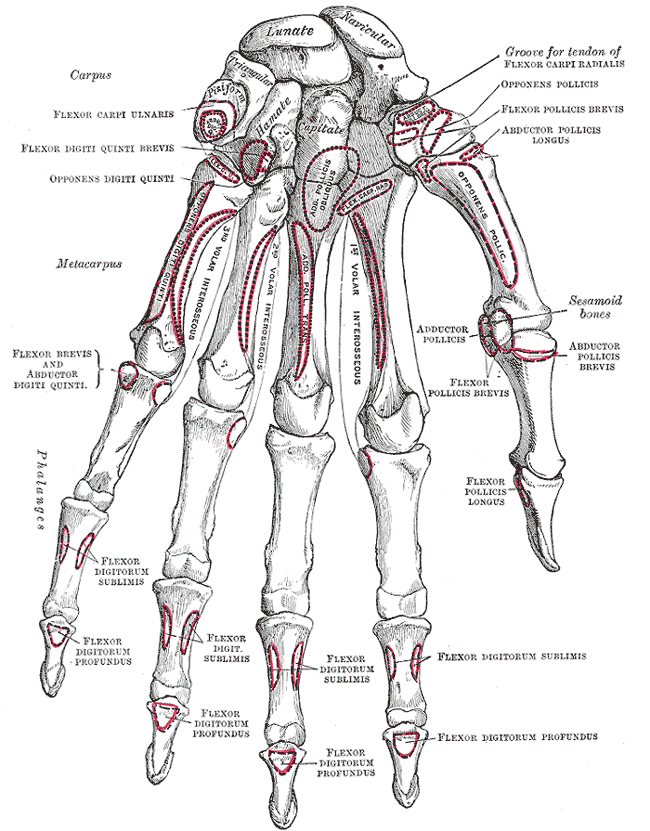
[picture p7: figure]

Fig. 3.1. Bones of the left hand (Volar Surface)

Tendons are white, flexible fibrous cords at the ends of muscles that attach the muscles to the radius, ulna, carpals, metacarpals and phalanges. When the muscles contract, they pull on the tendons to move the bone. The tendons that run down our fingers are held in place by a series of ligaments, called pulleys that arch over the tendons forming a “tunnel-like” sheath. Normally, the tendons glide easily through the tunnel. Some tendons also serve as stabilizers.
A series of ligaments in a tunnel-like arrangement hold the tendons in place on the bones. A slippery coating, called tenosynovium, surrounds the tendons and keeps the tendons moving smoothly under the ligaments when the hand grasps objects.
3.2 | Modelling of the Spring Actuator
| Here the NiTi coils are used to perform the functionality of the muscles and tendons.
Two sets of springs of different turns are used. One set of springs represent the tendons on the forearm and the other represent the tendons on the palm side of the hand. Two different sets of springs of different turns are required because the springs counteract each other to produce the grasp and release action.
| The solid length (“SL”) of the spring is decided according to the length of the spring
in its austenite phase. When the gripper performs the grasp action the springs attached on the palm surface gets actuated to its austenite phase. According to the finger model described in section 3.3, then length of the spring in its various phases using the specifications defined in section 2.2.2 of Chapter 2 are as follows:

SR Cold, SR Hot: 14, 5

Length in austenite phase: 10mm

Solid Length: 2mm

Length in martensite phase: 28mm

Number of turns: 10

| Similarly, when the gripper performs the release action, the springs on the forearm
get actuated to its austenite phase. Hence the length for the second set of springs in their various phases based on the specifications described in section 2.2.2.2 and are given as follows:

SR Cold, SR Hot: 14, 5

Length in austenite phase: 22mm

Solid Length: 4.4mm

Length in martensite phase: 61.6mm

Number of turns: 21.67

3.3 | Modelling of the Fingers of the Gripper
| Inspired by the skeletal structure of the human hand, we present an antagonistic
actuation mechanism which utilises the NiTi coils as muscle fibers and tendons as discussed in the previous section. This approach is used in the modelling, fabrication and development of a three finger gripper that behaves similar to human hand.
| The three finger are designed to represent the index finger, middle finger and the
thumb of a human hand. The gripper produces a grasp and release action similar to a human hand on the passage of an electrical impulse. When an electrical impulse is passed, one set of the NiTi coil actuators contracts while the other set is relaxed. Depending upon which set of the actuators gets contracted the gripper performs the grasp or release action.

3.3.1 Designing of the Finger Link

| The human hand has a complex structure made up of 27 individual bones: 8 carpal
bones, 5 metacarpal bones and 14 finger bones (also called phalanges) are connected by joints and ligaments. [22] The hand can be viewed in three sections by joint function:
| • Carpus and wrist • Metacarpus • Fingers or phalanges
| The links in the robotic gripper represent the phalanges and the metacarpus of a
human hand. But, unlike the human hand in which the phalanges and the metacarpus are of different sizes, the links used in the robotic gripper are of same shape and size. This has been done to reduce complexity and introduce symmetry in the model. The link is modelled using SolidWorks. Fig. 3.2 shows a model of the link with all its dimensions.

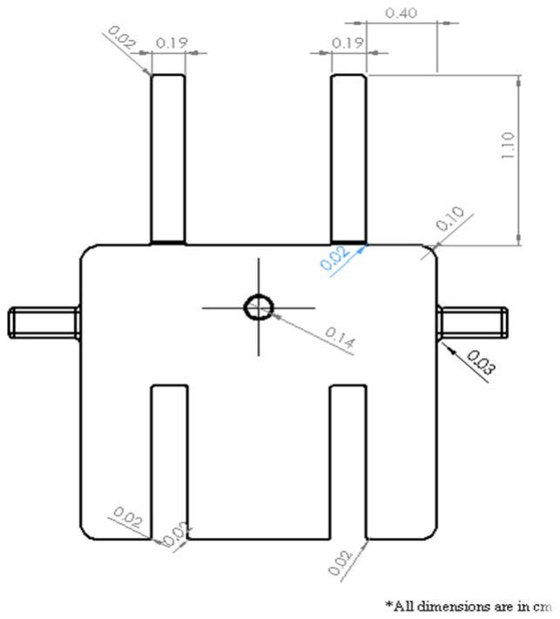
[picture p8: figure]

(a)

(b)

(c)

Fig. 3.2. The following figure represent the three views of the finger link (a) Front view. (b) Left view. (c) Top view.

3.3.2 Fabrication of the Links

The fabrication of the link includes the development of the link through a 3D printer. We used Ultimaker²

for the purpose of 3D printing. Ultimaker² is the successor
of Ultimaker Orignal [as seen in Fig. 3.3 (a)]which works on fused filament fabrication (FFF) printing technology. It uses a software Cura, which is the 3D model to toolpath Slicer. The printing filament used to create the 3D model for this project is PLA (Ploylactic acid) [Fig. 3.3 (b) shows a spool of PLA filament]. [23] PLA is a bio-degradable polymer that can be produced from lactic acid, which can be fermented from crops such as maize. PLA is harder than ABS, melts at a lower temperature (around 180°C to 220°C) and has a glass transition temperature between 60-65°C. It does have a slightly higher coefficient of friction in the drive and transport than ABS, but this is more compensated for by its lower viscosity when molten.

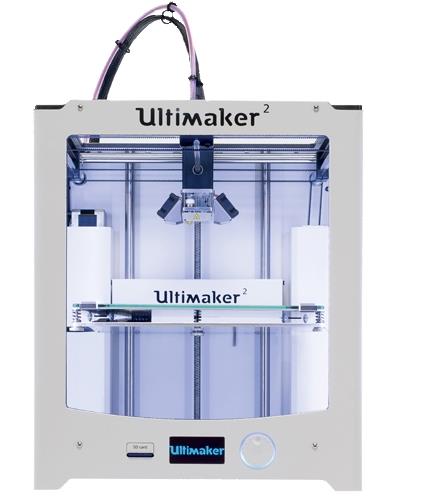
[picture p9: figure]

(a)

(b)

Fig. 3.3. (a) Ultimaker2 used for 3D printing (b) Spools of PLA, used as the printing filament.

The NiTi springs during a phase transformation from martensite to austenite on actuation reach a temperature of around 70°C. At such a high temperature the model could rupture and break as PLA reaches its glass transition temperature. Thus to avoid this, the whole model is wrapped around with a high temperature tape. We used Kapton tape which is made from Kapton® polyimide film with silicon adhesive. They are compatible with a wide range of temperatures as low as -269°C and as high as 260°C. Thus they act as thermal insulators and protect the model from the NiTi coils during its actuation.

3.3.3 Construction of the Finger of the Gripper

The human hand consist of phalanges (fingers) and metacarpus. Each finger has three individual bones of different lengths. Construction of the fingers of the gripper in the similar fashion is a tough challenge, since links of different lengths would require springs of different number of coils. This increases the cost of the springs to a great extent. Hence a sustainable solution to the problem has been proposed. Unlike the bones of the human hand, all the links of the gripper will be of same shape and length. This helped in reducing the cost of the springs by a factor of approximately 80.
The finger of the gripper consists of four links. Three representing the phalanges and one the metacarpus. Fig. 3.5 shows a fully constructed finger of the gripper. The links are connected to each other by attaching the extrusion, marked as (a) in the Fig. 3.4, of one link to the section marked as (b) of the other link. When the Hole 1 [See Fig. 3.4] of one link is aligned in parallel with the Hole 2 of the other link, a wire is passed through these holes to provide movement to the link. Finally, the links are joined together through screws.

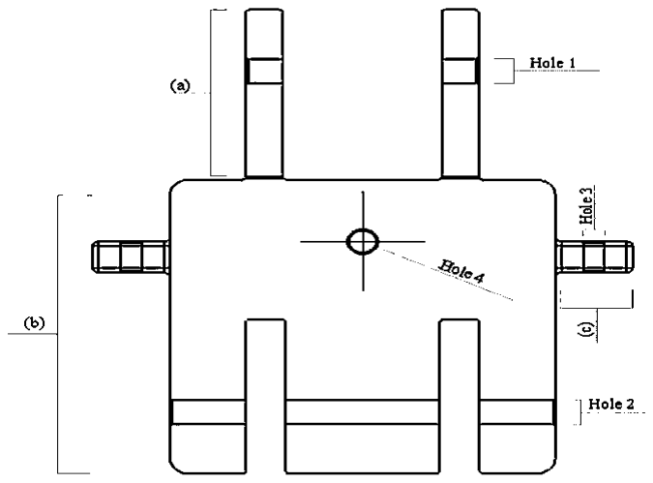
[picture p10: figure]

Fig. 3.4. Representation of the various components in the link model.

As discussed earlier in section 3.3, we require two sets of springs of different number of coils. The NiTi coils of solid length 4.4mm, are attached to the forearm side [See Fig. 3.2 (b)] of the link while the coils of solid length 2mm are connected to palm side of the link. The NiTi coils are attached between two links. One end of the NiTi muscle coil is fixed in Hole 4 [See Fig. 3.4] of one link and the other end is fixed in the Hole 4 of the other link.

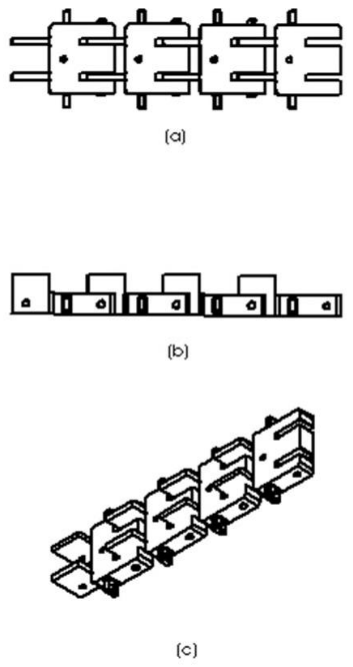
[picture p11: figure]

Fig. 3.5. Assembly of links to form a finger (a) Front view. (b) Left View. (c) Isometric View

The Fig. 3.5 represents an assembly of links joined together to form a finger of the gripper. As we can see in Fig. 3.5 (b), representing the left view of the finger, the extrusion on the forearm side of part (a) [as shown in Fig. 3.5], would help the finger to return and stay in a straight alignment during release action. Further, the last link to the finger is permanently fixed to the base of the gripper (discussed in next section).

3.3.4 Designing and Modelling of the Gripper Base

In biology, dactyly is the arrangement of digits (fingers and toes) on the hands, feet, or sometimes wings of a tetrapod animal. It comes from the Greek word δακτυλος = "finger”. Sometimes the ending "-dactylia" is used. The derived adjectives end with "-dactyl" or "-dactylous". Anisodactyl is the most common arrangement of digits in birds, with three toes forward and one back. This is common in songbirds and other perching birds, as well as hunting birds like eagles, hawks, and falcons.
The arrangement of fingers in the robotic gripper is inspired by those of anisodactyl. The only difference is that instead of having three forward fingers, our gripper has only two forward fingers and one finger at the back. Three fingers are symmetrically placed such that the back finger is in between the two forward fingers [See Fig. 3.6 (a)]. The model of the base of the gripper (as shown in Fig. 3.6) was developed using SolidWorks.

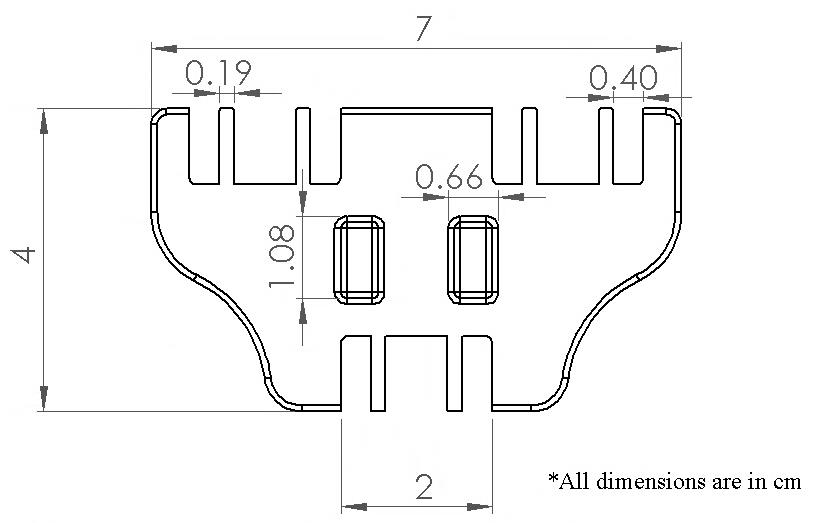
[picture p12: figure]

(a)

(b)

(c)

Fig. 3.6. Model of the base of the gripper. (a) Top View. (b) Front View. (c) Left View.

The extrusion seen in Fig. 3.6 (b), of 1 cm length and 0.50 cm thickness, has been provided so that an external arm can be connected to the gripper. The hole in Fig. 3.6 (c) is used to connect the T joint of the arm to the base of the gripper using a M3 type screw. Hence the robotic gripper can be either used independently or combined with a robotic arm for complex operations. The base of the gripper is 3D printed using Ultimaker² using PLA as the printing filament.

3.4 | Assembling of the Three Finger Gripper
| The Fig. 3.7(a) shows the fully connected fingers of the gripper. The NiTi coil
actuators are jointed on both sides of each finger using screws. The finger links are wrapped in Kapton tape to prevent any direct contact of the spring with the links. The links are connected to each other using a wire and screws, which not only holds the links together but also provides easy movement of the links in the vertical direction.

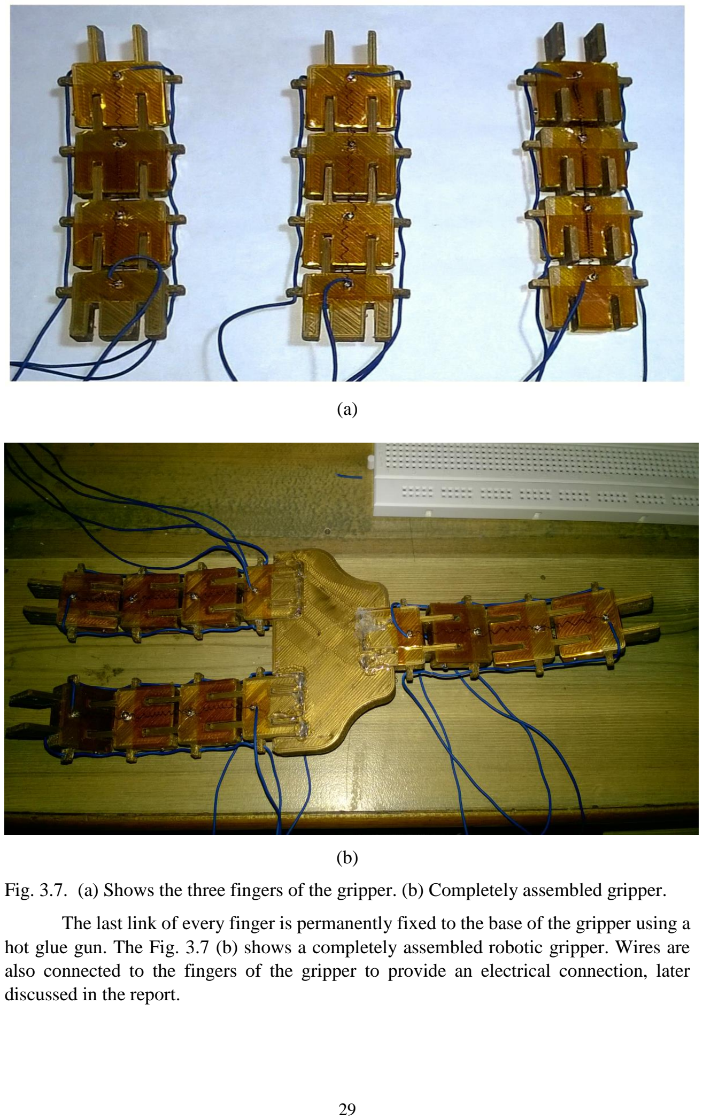
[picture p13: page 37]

(a)

(b)

Fig. 3.7. (a) Shows the three fingers of the gripper. (b) Completely assembled gripper.

The last link of every finger is permanently fixed to the base of the gripper using a hot glue gun. The Fig. 3.7 (b) shows a completely assembled robotic gripper. Wires are also connected to the fingers of the gripper to provide an electrical connection, later discussed in the report.

Chapter 4.
HARDWARE AND SOFTWARE SPECIFICATIONS
4.1 | Hardware Specifications
| The NiTi coils require constant current of 0.7A for two seconds, as stated in section
2.2.2.2, for actuation. Hence the gripper requires a circuit that can control the current for two seconds and then turn the supply off on demand in order to achieve the grasp and release motion. The following are the components required for construction of such a circuit:
| • Tiva™ TM4C123GH6PM Microcontroller from Texas Instruments. • BC368 NPN Transistors. • LM2596 DC-DC Buck Converter Step-Down Power Module. • Resistors of 1Ω and 2Ω resistances. • 11.1V 5Ah (55.5Wh) Li-Ion Battery. • Breadboard. • Jumper wires.

4.1.1 BC368 NPN General Purpose Amplifier

[25] This device is designed for general purpose medium power amplifiers and switches requiring collector currents to 1.5 A. Fig. 4.1 shows the BC368 NPN transistor with its configuration. Below are the ratings and characteristics associated with BC368.
| Absolute Maximum Ratings*

TA = 25°C unless otherwise noted
Symbol | Parameter | Value | Units
VCEO | Collector-Emitter Voltage | 20 | V
VCES | Collector-Base Voltage | 25 | V
VEBO | Emitter-Base Voltage | 5.0 | V
IC | Collector Current - Continuous | 2.0 | A
TJ, Tstg | Operating and Storage Junction Temperature Range | -55 to +150 | °C

*These ratings are limiting values above which the serviceability of any semiconductor device may be impaired.

NOTES:
1. These ratings are based on a maximum junction temperature of 150 degrees C.
2. These are steady state limits. The factory should be consulted on applications involving pulsed or low duty cycle operations.

Thermal Characteristics

TA = 25°C unless otherwise noted
Symbol | Characteristic | Max | Units
| | BC368
PD | Total Device Dissipation Derate above 25°C | 625 5.0 | mW mW/°C
RθJC | Thermal Resistance, Junction to Case | 83.3 | °C/W
RθJA | Thermal Resistance, Junction to Ambient | 200 | °C/W

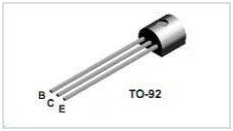
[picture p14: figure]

Fig. 4.1. BC368 NPN General Purpose Amplifier with its Base, Collector and Emitter marked as B, C and E respectively.

Electrical Characteristics

TA = 25°C unless otherwise noted
Symbol | Parameter | Test Condition | Min | Max | Units

OFF CHARATERISTICS
V(BR)CEO | Collector-Emitter Breakdown Voltage | IC = 10mA, IB = 0 | 20 | | V
V(BR)CES | Collector-Base Breakdown Voltage | IC = 10µA, IE = 0 | 25 | | V
V(BR)EBO | Emitter-Base Breakdown Voltage | IE = 10µA, IC = 0 | 5.0 | | V
ICBO | Collector-Cutoff Current | VCB = 25V, IE = 0 VCB = 25V, IE = 0, TA = 150°C | | 10 1.0 | µA mA
IEBO | Emitter-Cutoff Current | VEB = 5.0V, IC = 0 | | 10 | µA

ON CHARATERISTICS
hFE | DC Current Gain | IC = 5.0mA, VCE = 10V IC = 0.5A, VCE = 1.0V IC = 1.0A, VCE = 1.0V | 50 85 60 | 375
VCE(sat) | Collector-Emitter Saturation Voltage | IC = 1.0A, IB = 100mA | | 0.5 | V
VBE(on) | Base-Emitter On Voltage | IC = 1.0A, VCE = 1.0V | | 1.0 | V

SMALL SIGGNAL CHARATERISTICS
fT | Current | Gain-
Bandwidth Product

IC = 10mA, VCE = 5.0V,
f=35MHz

4.1.2 Tiva™ TM4C123GH6PM Microcontroller

[25] Texas Instrument's Tiva™ C Series microcontrollers provide designers a high-performance ARM® Cortex™-M-based architecture with a broad set of integration capabilities and a strong ecosystem of software and development tools. Targeting performance and flexibility, the Tiva™ C Series architecture offers an 80 MHz Cortex-M with FPU, a variety of integrated memories and multiple programmable GPIO. Tiva™ C Series devices offer consumers compelling cost-effective solutions by integrating application-specific peripherals and providing a comprehensive library of software tools which minimize board costs and design-cycle time.
The Tiva™ C Series ARM Cortex-M4 microcontrollers provide top performance and advanced integration. The product family is positioned for cost-conscious applications requiring significant control processing and connectivity capabilities such as:
- Low power, hand-held smart devices
- Gaming equipment
- Home and commercial site monitoring and control
- Motion control
- Medical instrumentation
- Test and measurement equipment
- Factory automation
- Fire and security
- Smart Energy/Smart Grid solutions
- Intelligent lighting control
- Transportation

For applications requiring extreme conservation of power, the TM4C123GH6PM microcontroller features a battery-backed Hibernation module to efficiently power down the TM4C123GH6PM to a low-power state during extended periods of inactivity. With a power-up/power-down sequencer, a continuous time counter (RTC), multiple wake-from-hibernate options, a high-speed interface to the system bus, and dedicated battery-backed memory, the Hibernation module positions the TM4C123GH6PM microcontroller perfectly for battery applications.
In addition, the TM4C123GH6PM microcontroller offers the advantages of ARM's widely available development tools, System-on-Chip (SoC) infrastructure IP applications, and a large user community. Additionally, the microcontroller uses ARM's Thumb®-compatible Thumb-2 instruction set to reduce memory requirements and, thereby, cost. Finally, the TM4C123GH6PM microcontroller is code-compatible to all members of the extensive Tiva™ C Series; providing flexibility to fit precise needs.

4.1.2.1 TM4C123GH6PM Microcontroller Overview

The TM4C123GH6PM microcontroller combines complex integration and high performance with the features shown in figure below [25].

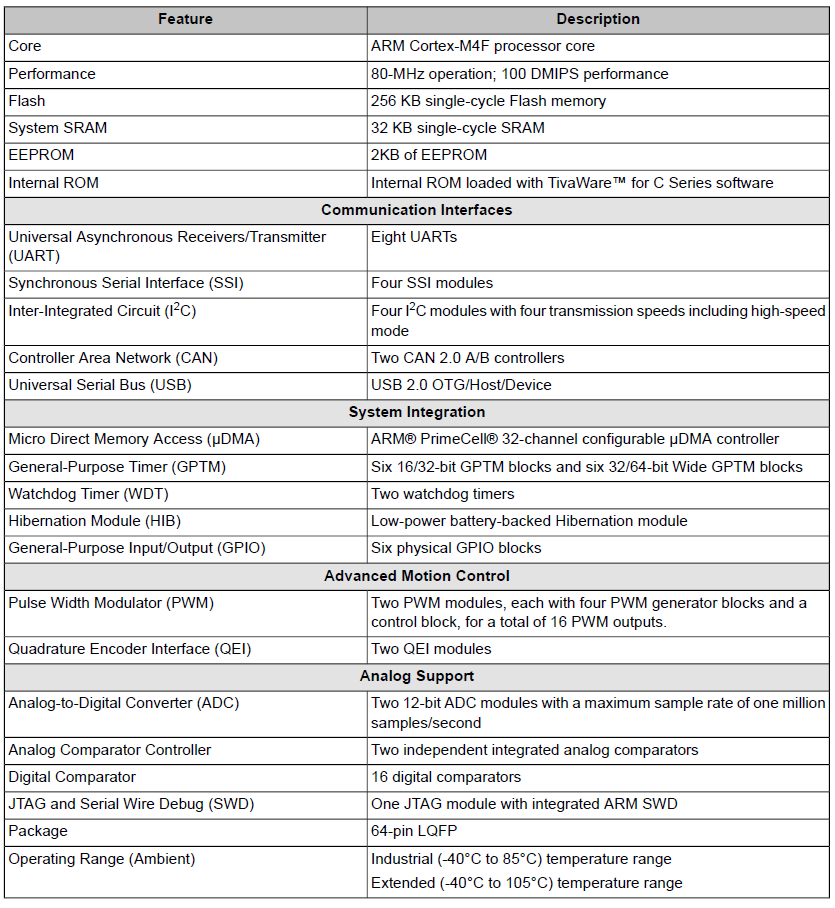
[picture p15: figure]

Fig. 4.2. Table showing the features of TM4C123GH6PM Microcontroller

4.1.2.2 TM4C123GH6PM Microcontroller Pin Structure

Fig. 4.3 draws the I/O port structure for the TM4C123GH6PM. This microcontroller is used on the EK-TM4C123GXL Launchpad. [26] Pins on the LM3S family have two possibilities: digital I/O or an alternative function. However, pins on the TM4C family can be assigned to as many as eight different I/O functions. Pins can be configured for digital I/O, analog input, timer I/O, or serial I/O. For example PA0 can be digital I/O or serial input. There are two buses used for I/O. The digital I/O ports are connected to both the advanced peripheral bus and the advanced high-performance bus. Because of the multiple buses, the microcontroller can perform I/O bus cycles simultaneous with instruction fetches from flash ROM. The TM4C123GH6PM has eight UART ports, four SSI ports, four I2C ports, two 12-bit ADCs, twelve timers, a CAN port, and a USB interface. The TM4C123GH6PM adds up to 16 PWM outputs. There are 43 I/O lines. There are twelve ADC inputs; each ADC can convert up to 1M samples per second.

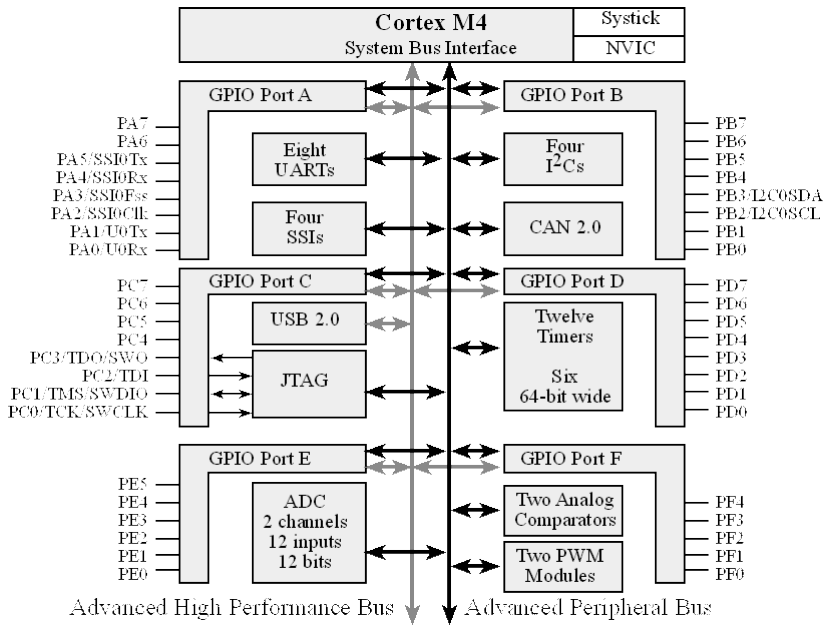
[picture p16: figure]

Fig. 4.3. I/O port pins for the TM4C123GH6PM microcontroller.

Each pin has one configuration bit in the GPIOAMSEL register. We set this bit to connect the port pin to the ADC or analog comparator. For digital functions, each pin also has four bits in the GPIOPCTL register, which we set to specify the alternative function for that pin (0 means regular I/O port). Not every pin can be connected to every alternative function.
Pins PC3 – PC0 were left off table in Fig. 4.2 because these four pins are reserved for the JTAG debugger and should not be used for regular I/O. Notice, most alternate function modules (e.g., U0Rx) only exist on one pin (PA0). While other functions could be mapped to two or three pins (e.g., CAN0Rx could be mapped to one of the following: PB4, PE4, or PF0.)
For example, if we wished to use UART7 on pins PE0 and PE1, we would set bits 1, 0 in the GPIO_PORTE_DEN_R register (enable digital), clear bits 1, 0 in the GPIO_PORTE_AMSEL_R register (disable analog), set the PMCx bits in the GPIO_PORTE_PCTL_R register for PE0, PE1 to 0001 (enable UART functionality), and set bits 1, 0 in the GPIO_PORTE_AFSEL_R register (enable alternate function). If we wished to sample an analog signal on PD0, we would set bit 0 in the alternate function select register, clear bit 0 in the digital enable register (disable digital), set bit 0 in the analog mode select register (enable analog), and activate one of the ADCs to sample channel 7.

4.1.2.3 Tiva LaunchPad based on the TM4C123GH6PM

The LaunchPad evaluation board (Figure 4.4) is a low-cost development board available as part number EK-LM4F120XL and EK-TM4C123GXL. The microcontroller board provides an integrated In-Circuit Debug Interface (ICDI), which allows programming and debugging of the on board LM4F120 or TM4C123 microcontroller. [26] One USB cable is used by the debugger (ICDI), and the other USB allows the user to develop USB applications (device). The user can select board power to come from either the debugger (ICDI) or the USB device (device) by setting the Power selection switch.

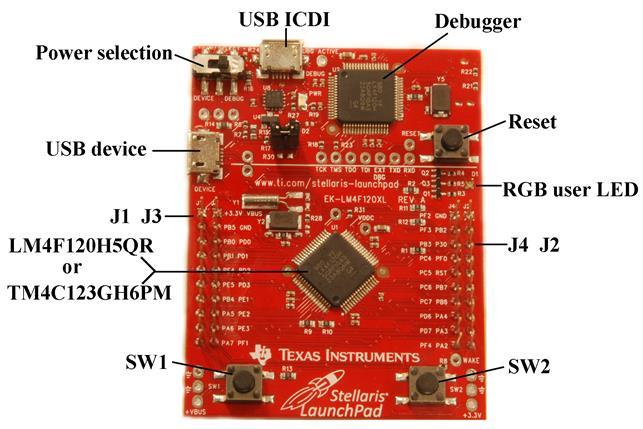
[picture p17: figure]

Fig. 4.4. Tiva LaunchPad based on the TM4C123GH6PM.

Pins PA1 – PA0 create a serial port, which is linked through the debugger cable to the PC. The serial link is a physical UART as seen by the LF4F120/TM4C and mapped to a virtual COM port on the PC. The USB device interface uses PD4 and PD5. The JTAG debugger requires pins PC3 – PC0. The LaunchPad connects PB6 to PD0, and PB7 to PD1. If you wish to use both PB6 and PD0 you will need to remove the R9 resistor. Similarly, to use both PB7 and PD1 remove the R10 resistor.

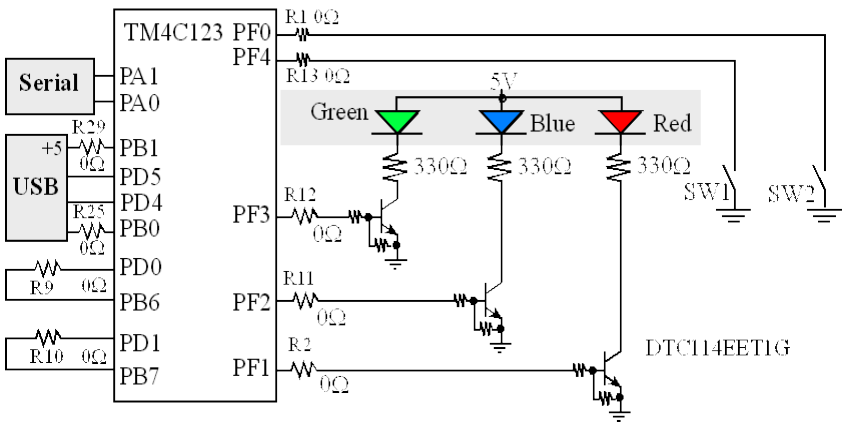
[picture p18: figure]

Fig. 4.5. Switch and LED interfaces on the Tiva LaunchPad Evaluation Board. The zero ohm resistors can be removed so the corresponding pin can be used for its regular purpose.

The Tiva LaunchPad evaluation board has two switches and one 3-color LED. See Fig. 4.5. The switches are negative logic and will require activation of the internal pull-up resistors. In particular, you will set bits 0 and 4 in GPIO_PORTF_PUR_R register. The LED interfaces on PF3 – PF1 are positive logic. To use the LED, make the PF3 – PF1 pins an output. To activate the red colour, output a one to PF1. The blue colour is on PF2, and the green colour is controlled by PF3. The 0-Ω resistors (R1, R2, R11, R12, R13, R25, and R29) can be removed to disconnect the corresponding pin from the external hardware.

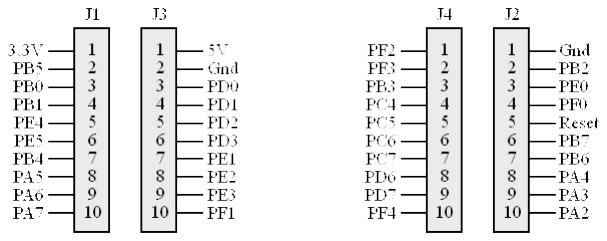
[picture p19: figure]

Fig. 4.6. Interface connectors on the Tiva TM4C123 LaunchPad Evaluation Board. The LaunchPad has four 10-pin connectors, labelled as J1 J2 J3 J4 in Fig. 18 and Fig. 4.6, to which you can attach your external signals. The top side of these connectors has male pins, and the bottom side has female sockets. The intent is to stack boards together to make a layered system. Texas Instruments also supplies Booster Packs, which are pre-made external devices that will plug into this 40-pin connector. The Booster Packs for the MSP430 LaunchPad are compatible with this board. One simply plugs the 20-pin connectors of the MSP430 booster into the outer two rows. The inner 10-pin headers (connectors J3 and J4) apply only to Stellaris or Tiva Booster Packs.

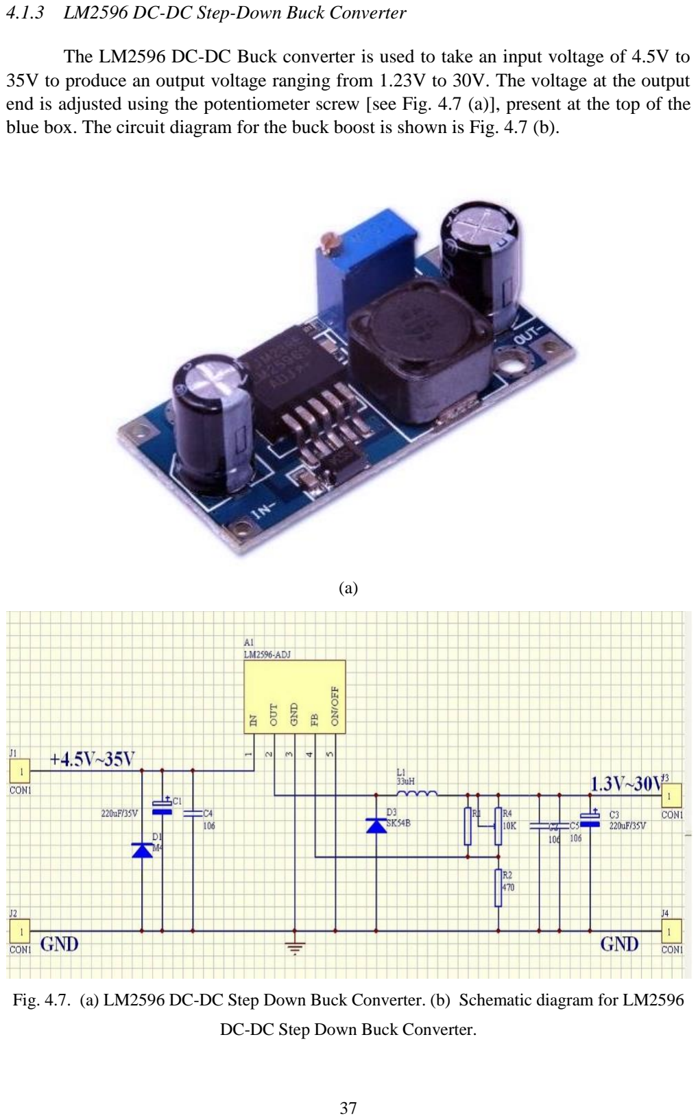
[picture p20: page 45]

4.1.3 LM2596 DC-DC Step-Down Buck Converter

The LM2596 DC-DC Buck converter is used to take an input voltage of 4.5V to 35V to produce an output voltage ranging from 1.23V to 30V. The voltage at the output end is adjusted using the potentiometer screw [see Fig. 4.7 (a)], present at the top of the blue box. The circuit diagram for the buck boost is shown is Fig. 4.7 (b).

(a)

Fig. 4.7. (a) LM2596 DC-DC Step Down Buck Converter. (b) Schematic diagram for LM2596

DC-DC Step Down Buck Converter.

The buck boost is used to step down the 11.1V from the Li-ion battery module, to produce a voltage of 9.5V to be supplied to the gripper circuit. The specification of the buck boost are given in the table below [27].

Basic Attributes
Module Property | Non-isolation buck | Rectification mode | Synchronous rectifier
Input voltage | 4V-35V | Output Voltage | 1.23V-30V
Input current | 3A (maximum) | Conversion efficiency | 92% (highest)
Switching frequency | 150KHz | Output ripple | 30mV (maximum)
Load regulation | ± 0.5% | Voltage regulation | ± 2.5%
Work temperature | -40 - +85 | Overall dimension | 48*23*14(L*W*H)(mm)
4.2 | Software Specifications
| The project required the use of three softwares in all for development of a working
prototype of the robotic gripper using NiTi coils. The softwares were used for designing, fabrication and developing a control circuit for the gripper. The following softwares were used:
| • SolidWorks® 3D Cad Software • Cura 3D Printing Slicing Software • µVision® IDE (Integrated Development Environment) from Keil Software
| SolidWorks was used for designing of the finger links and the base of the gripper, and
has been discussed in section 3.3. The software Cura was used during fabrication of the links and the base of gripper through the 3D printer. The µVision® IDE combines project management, run-time environment, build facilities, source code editing, and program debugging in a single powerful environment. It is for programming of the microcontroller discussed in section 4.1.2.

4.2.1 Code for the microcontroller

#include "tm4c123gh6pm.h"

#include "Port_Init.h"

// ***** 2. Global Declarations Section *****

#define SYSCTL_RCGC2_R | (*((volatile unsigned long *)0x400FE108))

#define GPIO_PORTE_DATA_R | (*((volatile unsigned long *)0x400243FC))

#define GPIO_PORTE_DIR_R | (*((volatile unsigned long *)0x40024400))

#define GPIO_PORTE_AFSEL_R | (*((volatile unsigned long *)0x40024420))

#define GPIO_PORTE_DEN_R | (*((volatile unsigned long *)0x4002451C))

#define GPIO_PORTE_AMSEL_R | (*((volatile unsigned long *)0x40024528))

#define GPIO_PORTE_PCTL_R | (*((volatile unsigned long *)0x4002452C))

#define GPIO_PORTF_DATA_R | (*((volatile unsigned long *)0x400253FC))

#define GPIO_PORTF_DIR_R | (*((volatile unsigned long *)0x40025400))

#define GPIO_PORTF_AFSEL_R | (*((volatile unsigned long *)0x40025420))

#define GPIO_PORTF_PUR_R | (*((volatile unsigned long *)0x40025510))

#define GPIO_PORTF_DEN_R | (*((volatile unsigned long *)0x4002551C))

#define GPIO_PORTF_LOCK_R | (*((volatile unsigned long *)0x40025520))

#define GPIO_PORTF_CR_R | (*((volatile unsigned long *)0x40025524))

#define GPIO_PORTF_AMSEL_R | (*((volatile unsigned long *)0x40025528))

#define GPIO_PORTF_PCTL_R | (*((volatile unsigned long *)0x4002552C))

#define SYSCTL_RCGC2_R | (*((volatile unsigned long *)0x400FE108))

unsigned long in;

// FUNCTION PROTOTYPES: Each subroutine defined

void DisableInterrupts(void); // Disable interrupts

void EnableInterrupts(void); // Enable interrupts

void delayms(unsigned long);// Delay function

// ***** 3. Subroutines Section *****

void PortE_Init(){volatile unsigned long delay;

SYSCTL_RCGC2_R |= 0x00000010;

delay = SYSCTL_RCGC2_R;

GPIO_PORTE_DIR_R |= 0x06;

GPIO_PORTE_AFSEL_R &= ~0x06;

GPIO_PORTE_AMSEL_R &= ~0x06;

GPIO_PORTE_PCTL_R &= ~0x00000FF0;

GPIO_PORTE_DEN_R |= 0x06;

}

void PortF_Init(){volatile unsigned long delay;

SYSCTL_RCGC2_R |= 0x00000020;

delay = SYSCTL_RCGC2_R;

GPIO_PORTF_LOCK_R = 0x4C4F434B;

GPIO_PORTF_CR_R = 0x11;

GPIO_PORTF_DIR_R &= ~0x11;

GPIO_PORTF_AMSEL_R &= ~0x11;

GPIO_PORTF_AFSEL_R &= ~0x11;

GPIO_PORTF_DEN_R |= 0x11;

GPIO_PORTF_PCTL_R &= ~0x0000000F;

GPIO_PORTF_PUR_R |= 0x11;

int main(void){

unsigned long volatile delay;

TExaS_Init(SW_PIN_PE0, LED_PIN_PE1); | // Set system clock to 80 MHz
PortE_Init(); | // Initialising PE1 and PE2 on PortE
PortF_Init(); | // Initialising the two switches on PortF
while(1){
if(GPIO_PORTF_DATA_R == 0x01){ | // check if switch 1 pressed
while(GPIO_PORTF_DATA_R == 0x01)
GPIO_PORTE_DATA_R |= 0x02; | // Opening Port E1
GPIO_PORTE_DATA_R &= ~0x02; | // Closing Port E1
delayms(3000); | // Cooling deformation delay
}
else if(GPIO_PORTF_DATA_R == 0x10){ | // check if switch 2 pressed
GPIO_PORTE_DATA_R |= 0x04; | // Enable Port E pin2
delayms(2000); | // delay for 2 seconds
GPIO_PORTE_DATA_R &= ~0x04; | // Closing Port E pin2
delayms(3000); | // Cooling deformation delay
}
else{
GPIO_PORTE_DATA_R &= ~0x06;
// Close PE1 and PE2 otherwise }
}
}

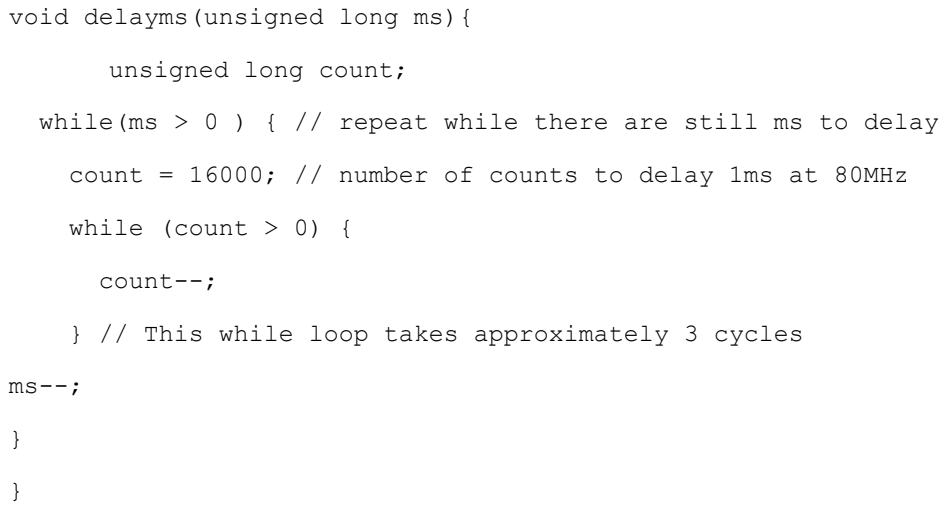
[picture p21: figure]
void delayms(unsigned long ms){; unsigned long count;; while (count > 0) {; count--;

4.3 | Control Circuit for the Gripper
| A control circuit is required to control the grasp and release motion of the robotic
gripper. The control circuit basically controls the current through the NiTi coils, hence controlling its actuation. Fig. 4.8 represents the control circuit for the robotic gripper.

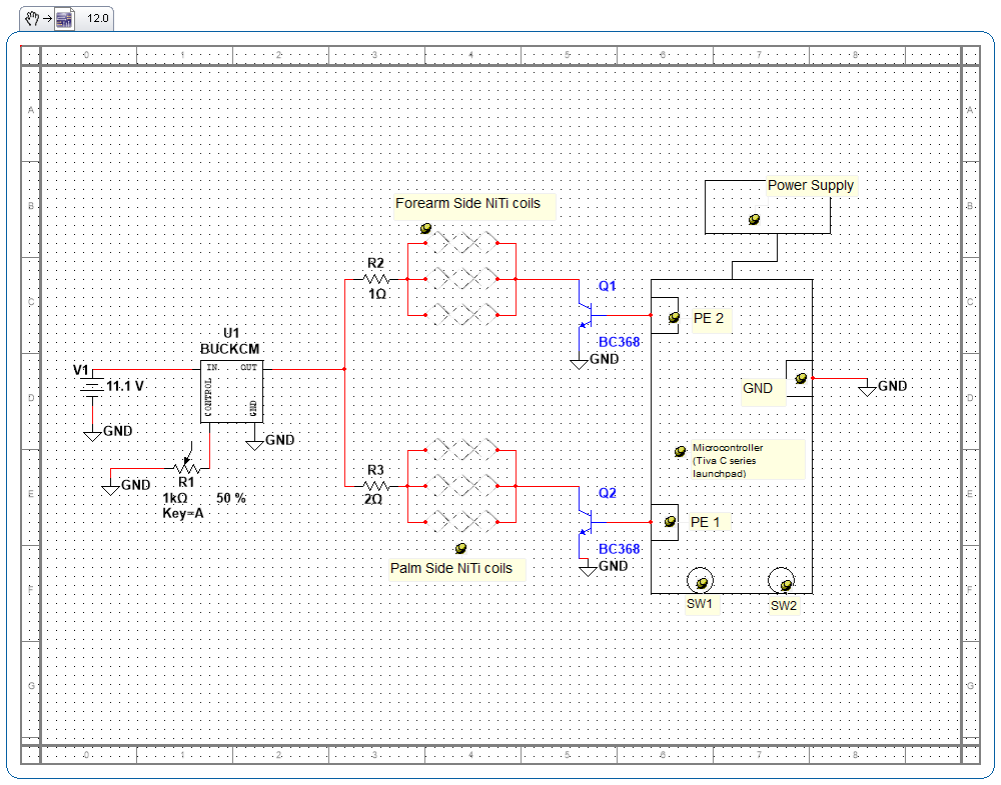
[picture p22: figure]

Fig. 4.8. Control circuit for the robotic gripper while(ms > 0 ) { // repeat while there are still ms to delay

count = 16000; // number of counts to delay 1ms at 80MHz

} // This while loop takes approximately 3 cycles

[See Fig. 4.8] The control circuit consists of an 11.1 V Li-ion battery module represented by V1. It is further connected to a buck converter (represented as U1), which has an adjustable potentiometer (represented as R1). The value of R1 is adjusted so that the buck converter supplies a voltage of 9.5 V. The output of the buck converter is connected to R2 and R3, which in turn are connected in parallel. R2 is connected to the NiTi coils on the forearm side of the gripper, while R3 is connected to the palm side of the gripper. The NiTi coils on each side of the two resistors are connected in parallel to each other.
The NiTi coils on forearm side and palm side are further connected to the collector of the NPN transistors Q1 and Q2 respectively. The emitter end of the two transistors are connected to ground. The base of the two transistors Q1 and Q2 are connected to Port E pin1 and Port E pin2 of the microcontroller respectively. The switches SW1 and SW2 represent the Port F pin0 and Port F pin4 respectively of the microcontroller. These are tactile switches are embedded on the LaunchPad itself. The values of R2 and R3 are selected such that when the NiTi coils are actuated, a current of approximately 0.7 A runs through them. The GND pin on the microcontroller provides the ground terminal to the circuit.

Chapter 5.
WORKING OF THE PROJECT
5.1 | Analogy between the Gripping by Human Hand and the Robotic Gripper
| The hand has a very delicate and complex structure. This allows muscles and joints
in the hand a great range of movement and precision. The different forces are also distributed in the hand in the best possible way. But the hand is also quite vulnerable: tendons, nerve fibers, blood vessels and very thin bones are all positioned right under the skin and are only protected by a thin layer of muscle and fat. Only the palm is protected by a strong pad of tendons (aponeurosis) for a powerful grip.
| To grasp and move objects, the hand has two different ways of gripping things: • Power grip • Precision grip. The technique used depends on whether the object is very large and very heavy,

and what sort of shape it has and how easy it is to handle. The power grip is better suited for large, heavy objects, and the precision grip is used for small, lighter objects.

5.1.1 Power Grip

[22] The power grip is used for carrying heavy bags or for holding on to a handle, for example. In the power grip, the object is held in the palm of the hand, the long flexor tendons pull the fingers and the thumb so that they can tightly close around the object. This grip is made possible by the four other fingers flexing and, more importantly, the ability of the thumb to be positioned opposite the fingers. With the hand in this position, larger objects such as a stone or a heavy bottle can be held and moved in a controlled way. The greater the weight and the smoother the surface is, the more strength is needed for holding and moving the object.
| The robotic gripper also uses the same technique for gripping of larger objects. The
palm of the hand is represented by the base of the gripper and the tendons represent the NiTi coils. Since the robotic gripper is a three finger gripper, hence during the grasp motion, the two fingers flex together with the third finger acting as the thumb, situated opposite to the two fingers help in gripping an object similar to the human hand.

5.1.2 Precision Grip

| The precision grip is important for delicately handling and moving an object, for
example when writing, sewing or drawing. When using the precision grip, the thumb and the index finger work like a forceps: The thumb is opposite one or more fingertips, allowing the hand a controlled grip of even very small objects like a pencil or fine instruments. Depending on the weight of the object and the direction and speed of the movement, the brain directs the use of force and coordinates the muscles of the hand.
| Although the current control circuit of the robotic gripper does not allow for
precision grip but it can be modified to provide the functionality of precision grip to the robotic gripper. Such a control circuit would require to actuate each finger independently and hence the combination of any two can be used to provide precision grip.

5.2 | Implementation of the Robotic Gripper
| The control circuit [See Fig. 4.8] is designed in a way such that the gripper can
perform grasp and release motion. With the current control circuit, the gripper can only perform a power grip. The grasp and release motion performed by the gripper is controlled using the two switches SW1 and SW2, embedded on the microcontroller [See Fig. 5.1]. The Fig. 5.1 (a), represents the control circuit during grasp motion of the microcontroller. The functionality of the griper is such that as long as the SW1 on the microcontroller is pressed Port E pin 1 is open and a current flows through it.
| This in turn activates the base of the NPN transistor Q2 and the collector and emitter
of Q2 get electrically connected. As a result the NiTi coils on the palm side of the gripper get connected to the ground and a current flows through them. A current of 0.7A flows through each finger of the gripper and a result the NiTi coils get actuated and gets transformed to their austenite phase. As a result the finger links flexes towards each other, which in turn results in the gripping action of the robotic gripper. It should be noted that switch SW1 should be pressed for at least two seconds for the gripper to perform the gripping action. This is because the NiTi coils require a current of 0.7A for at least two seconds for complete phase transformation.

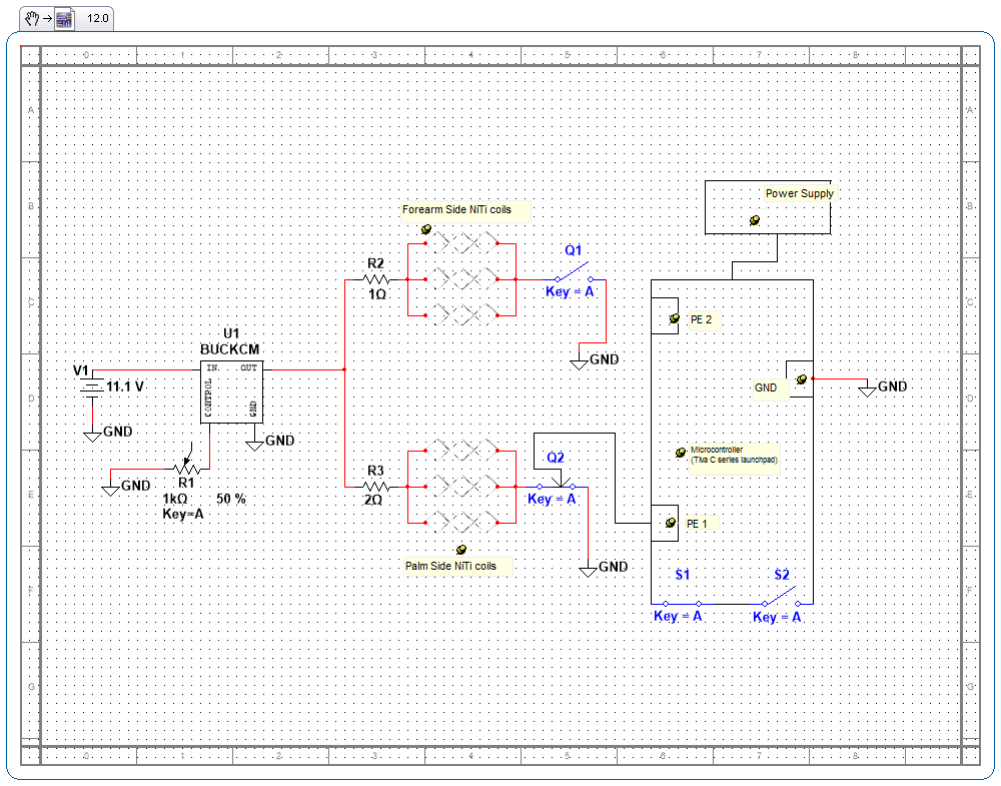
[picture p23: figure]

(a)

(b)

Fig. 5.1. (a) Control circuit during grasp action of the robotic gripper. (b) Control circuit during the release action of the robotic gripper

Similarly, when switch SW2 on the microcontroller is pressed, Port E pin 2 is opened [See Fig. 5.1 (b)] for a period of two seconds. This in turn activates the base of transistor Q1 and its collector gets connected to its emitter. Hence the NiTi coils on the forearm side are connected to ground. This in turn circulates a current of 0.7A in each finger (on the forearm side) of the gripper. This result in flexing of the links away from each other and the gripper performs the release action.
Since the Port E pin 2 was opened only for two seconds, hence the current in the coils also flows only for two seconds. This time is enough for the gripper to perform the release action and as well as prevents the NiTi coils from excessive heat produced by the current. There is also a three second delay after every grasp or release action of the gripper. This is because it takes about three seconds for the NiTi coils to cool down from its austenite to martensite phase after the current is removed. During the cooling deformation period of three seconds, neither of the switches are operational. This helps in preventing any permanent deformation in the NiTi coils.

Chapter 6.
RESULTS AND DISCUSSION

The Robotic gripper is fixed to a wooden arm through the hole present at back of the base of the gripper. The control circuit along with the microcontroller and the battery is connected to the wooden arm. The robotic gripper uses an open loop control to perform the grasp and release motion. When SW1 on the microcontroller is pressed the robotic gripper grasps the object. When SW2 on the microcontroller is pressed the robotic gripper releases the object. Fig.6.1 shows the gripping and release of an object by the robotic gripper.

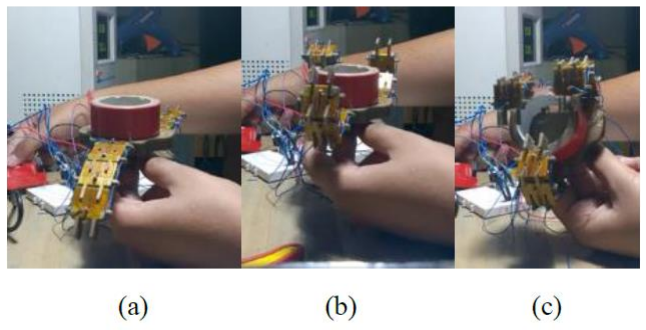
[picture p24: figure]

Fig.6.1. Gripper during the gripping of an object. (a) Gripper at rest. (b) Movement of fingers during gripping. (c) Full grip of the object.

6.1 | Advantages of the Developed System
| The use of NiTi coils as actuators provide better mechanical performance. Flexinol®
actuator wires are smaller by far than alternatives. At least 1,000 times smaller than solenoids for the same work done. Due to their small size, they make the gripper very light in weight. Flexinol® actuator springs can be used as it is, thus eliminating gear boxes, housings, bearings, and so on. Their flexible forgiving performance is easier to work with. Thus the robotic gripper has a simple circuit that can be easily modified. In corrosive environments Flexinol® actuator wires’ high corrosion resistance really pays off. Flexinol® actuator wires are inexpensive to buy and cost less and therefore helps in manufacturing a cheap robotic gripper.
| Using a Three Finger Gripper provides a greater flexibility and more reliability to
grip or grasp different kinds of parts. Since NiTi coils undergo a structural phase transformation when actuated, hence the robotic gripper provides a strong power grip till the switch is pressed. The NiTi coils have a lifetime of about million cycles, hence can be used for a long time. They doesn’t require any maintenance once installed, hence thus reduces the maintenance cost. Since the NiTi coils are attached only through a screw to the finger links, hence can be easily replaced when damaged. Since the fingers of the gripper are electrically connected in parallel [See Fig. 5.1], hence additional fingers can be added without altering the control circuit. The only modification required would be in the model of the base of the gripper where the fingers are finally attached.

6.2 | Limitations
| NiTi have many advantages over traditional actuators, but do suffer from a series
of limitations that may impede practical application.
| • Response time and response symmetry: SMA actuators are typically actuated electrically, where an electric current results in Joule heating. Deactivation typically occurs by free convective heat transfer to the ambient environment. Consequently, SMA actuation is typically asymmetric, with a relatively fast actuation time and a slow deactuation time. A number of methods have been proposed to reduce SMA deactivation time, including forced convection, [15] and lagging the SMA with a conductive material in order to manipulate the heat transfer rate.
| Novel methods to enhance the feasibility of SMA actuators include the use of a conductive "lagging". This method uses a thermal paste to rapidly transfer heat from the SMA by conduction. This heat is then more readily transferred to the environment by convection as the outer radii (and heat transfer area) is significantly greater than for the bare wire. This method results in a significant reduction in deactivation time and a symmetric activation profile. As a consequence of the increased heat transfer rate, the required current to achieve a given actuation force is increased. [16]
| • Structural fatigue and functional fatigue: NiTi is subject to structural fatigue – a failure mode by which cyclic loading results in the initiation and propagation of a crack that eventually results in catastrophic loss of function by fracture. The physics behind this fatigue mode is accumulation of microstructural damage during cyclic loading. This failure mode is observed in most engineering materials, not just SMAs. NiTi coils are also subject to functional fatigue, a failure mode not typical of most engineering materials, whereby the SMA does not fail structurally but loses its Shape memory characteristics over time. As a result of cyclic loading (both mechanical and thermal), the material loses its ability to undergo a reversible phase transformation. For example, the working displacement in an actuator decreases with increasing cycle numbers. The physics behind this is gradual change in microstructure—more specifically, the build-up of accommodation slip dislocations. This is often accompanied by a significant change in transformation temperatures. [18]
| • Unintentional Actuation: NiTi actuators are typically actuated electrically by Joule heating. If the NiTi is used in an environment where the ambient temperature is uncontrolled, unintentional actuation by ambient heating may occur.

Chapter 7.
CONCLUSION AND FUTURE SCOPE
7.1 | Conclusion
| This report demonstrated a Soft Robotic Gripper using NiTi coils as the actuators.
The development, modelling and fabrication of NiTi coil actuators has been discussed. The report well informs about the modelling and fabrication of the links of the finger and the base of the gripper, construction of the fingers using these links and assembling of the gripper as a whole. The control circuit used to control the grasp and release motion of the gripper has been briefly discussed.
| A detailed overview of the components and the software used in the process have
also been discussed. The phase transformation property of the NiTi coils when current is supplied to them, is used to produce the grasp and release movement of the links of the finger. The current control circuit of the gripper is designed only for power gripping. The circuit can be modified to produce a precision grip.
| The control circuit consists of a microcontroller that control the actuation of the NiTi
coils. The two switches on the on the microcontroller are used to perform the grasp and release action of the gripper. The whole setup is attached to wooden arm to provide a firm for the control circuit and hold the gripper during the grasp and release motion.
7.2 | Future Scope
| The three fingers robotic gripper can be extended to a full five finger gripper and
thus could replicate all the gestures performed by the human hand. This will also provide a much firmer grip on the object it grasps. The control circuit of the gripper can also be modified to produce precision grip, similar to that of the human hand. The design of the robotic gripper could be modified to design limbs of other animals.
| The technology used in the gripper, can be applied to a glove, which in turn could
be used to provide movement to the hands of a paralysed person. Similarly, it can be used to develop other wearables. The gripper can also be used to interface with the robotic arms used in industrial automation as means for a cheaper and better gripper.
| The robotic gripper can also be used to sync with a brain control interface and thus
one could control the gripper through his mind. The technology used to develop the robotic gripper can also be used to develop a robotic arm and other parts of the body.

REFERENCES

1. Monkman, G. J.; Hesse, S.; Steinmann, R.; Schunk, H. (2007). Robot Grippers. WileyVCH.p. 62. ISBN 9783527406197.
2. Fantoni, G., Santochi, M., Dini, G., Tracht, K., ScholzReiter,B., Fleischer, J., Lien, T.K., Seliger, G.,Reinhart, G.,Franke, J., Hansen, H.N., Verl, A.,2014, Grasping devices and methods in automated production processes, CIRP Annals Manufacturing Technology, Volume 63, Issue 2, 2014, Pages 679701, ISSN 00078506, http://dx.doi.org/10.1016/j.cirp.2014.05.006.
3. Biologically Inspired Robotics Wikipedia
4. Trivedi, D., Rahn, C. D., Kier, W. M., & Walker, I. D. (2008). Soft robotics: Biological inspiration, state of the art, and future research. Applied Bionics and Biomechanics, 5(3), 99117.
5. R. Shepherd, F. Ilievski, W. Choi, S. Morin, A. Stokes, A. Mazzeo, X. Chen, M. Wang, and G. Whitesides, “Multigait soft robot,” Proceedings of the National Academy of Sciences, vol. 108, no. 51, pp. 20400–20403, 2011.
6. "Robotics Grasping and Force closure" (PDF). pdf. FU Berlin. Retrieved 20140320.
7. Micro artificial muscle fiber using NiTi spring for soft robotics Sangbae Kim, Elliot Hawkes, Kyujin Choy, Matthew Joldaz, Joe Foleyz and Robert Wood Harvard Micro robotics Laboratory Harvard University, Cambridge, Massachusetts, Seoul National University Seoul, South Korea Government & Industrial Research iRobot Corporation Bedford, Massachusetts.
8. Bi-Chiau Chang, John Shaw, and Mark Iadicola. Thermodynamics of shape memory alloy wire: Modelling, experiments, and application. Continuum Mechanics and Thermodynamics, 18(1):83–118, 2006.
9. B. Kim, M.G. Lee, Y.P. Lee, Y. Kim, and G. Lee. An earthworm-like micro robot using shape memory alloy actuator. Sensors and Actuators, A: Physical, 125(2):429–437, 2006.
10. Hyo Jik Lee and Jung Ju Lee. Evaluation of the characteristics of a shape memory alloy spring actuator. Smart Materials and Structures, 9(6):817–823, 2000.
11. Y. Dong, Z. Boming, and L. Jun. A changeable aerofoil actuated by shape memory alloy springs. Materials Science and Engineering A, 485(1-2):243–250, 2008.
12. K.J. Cho, E. Hawkes, C. Quinn, and R.J. Wood. Design, fabrication and analysis of a body-caudal fin propulsion system for a micro robotic fish. In Proceedings -IEEE International Conference on Robotics and Automation, pages 706–711, 2008.
13. Tom C. Waram. Actuator Design Using Shape Memory Alloys. T.C. Waram, 1063 King St. W., Suite 204 Hamilton, Ontario L8S 1L8 Canada, second edition, 1993. Phone: (905)525-8251.
14. M. Dolce and D. Cardone, “Mechanical behaviour of shape memory alloys for seismic applications—1. Martensite and austenite NiTi bars subjected to torsion,” Int. J. Mech. Sci., vol. 43, pp. 2631–2656, Nov. 2001.
15. B. Chang, J. Shaw, and M. Iadicola, “Thermodynamics of shape memory alloy wire: Modelling, experiments, and application,” Continuum Mech. Thermodyn., vol. 18, no. 1, pp. 83–118, 2006.

16. Meshworm: A Peristaltic Soft Robot With Antagonistic Nickel Titanium Coil Actuators Sangok Seok, Cagdas Denizel Onal, Member, IEEE, Kyu-Jin Cho, Member, IEEE, Robert J. Wood, Daniela Rus, Fellow, IEEE, and Sangbae Kim.
17. Y. Liu, “Detwinning process and its anisotropy in shape memory alloys,” Proc. SPIE Smart Mater., vol. 4234, pp. 82–93, 2001.
18. K. Otsuka and C. M. Wayman, Shape Memory Materials. Cambridge, U.K.: Cambridge Univ. Press, 1998.
19. Technical data sheet of Flexinol, Dynalloy, Inc. makers of dynamic alloys.
20. HeathPages.org,http://www.healthpages.org/anatomyfunction/anatomyhandwrist/
21. Schmidt R, Lang F, Heckmann M. Physiologie des Menschen: mit Pathophysiologie. Heidelberg: Springer. 2011.
22. National | Library | of | Medicine | PubMed | Health,
http://www.ncbi.nlm.nih.gov/pubmedhealth/PMH0072546/
23. PLA RepRapWiki, http://reprap.org/wiki/PLA
24. BC368 NPN General Purpose Amplifier, Technical Datasheet, Fairchild Semiconductors.
25. Tiva™ TM4C123GH6PM Microcontroller Datasheet, Texas Instruments
26. Chapter 6: Parallel I/O, ports Embedded Systems: Introduction to ARM Cortex-M Microcontrollers, Jonathan Valvano and Ramesh Yerraballi, 2014, ISBN: 978-1477508992, http://users.ece.utexas.edu/~valvano/arm/outline1.htm
27. LM2596 DC-DC Step-Down Buck Converter Datasheet.

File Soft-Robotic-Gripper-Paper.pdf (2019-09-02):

Abstract—This paper presents the development and analysis of a soft robotic platform that exhibits the grasping and release action similar to a human hand. The design of the gripper is basically based on a human hand except for the fact that all the joint to joint distances in a finger of the robotic gripper are equal. Each finger is composed of four sub-components and three fingers are joint together to a base to form the hand. Nickel titanium (NiTi) coils (also known as Shape Memory Alloys) are used as the actuating medium and are placed across the joints of the finger. The finger sub-components are made of PLA using a 3D printer. The actuation of the nickel titanium coils is controlled through a constant current supply, which in turn is controlled through a switching circuit and a microcontroller. This approach allows for a simple, low cost, energy efficient gripper. The paper further discusses the potential use and application of this platform.

Index Terms—Robotic gripper, nickel titanium (NiTi) coil actuators, PLA, soft robotics, shape memory alloys (SMA).

I. INTRODUCTION
N robotics, an end effector is a device at the end of a robotic arm, designed to interact with the environment. The exact nature of this device depends upon the application of the robot. In wider sense, an end effector can be seen as the part of the robot that interacts with the work environment. End effectors may consist of a gripper or a tool. When referring to robotic prehension there are four general categories of robot grippers, these are [1]:
- Impactive – jaws or claws which physically grasp by direct impact upon the object.
- Ingressive – pins, needles or hackles which physically penetrate the surface of the object.
- Astrictive – suction forces applied to the objects surface.
- Contigutive – requiring direct contact for adhesion to take place.
They are based on different physical effects used to guarantee a stable grasping between a gripper and the object to be grasped. [2] Industrial grippers can be mechanical, the most diffused in industry, but also based on suction or on the magnetic force. The type of gripper discussed in this paper exploits both friction and form closure and hence can be

This work has been supported by Technology Information, Forecasting and Assessment Council (TIFAC Core), Ajay Kumar Garg Engineering College, Ghaziabad, India.
Shubham Gupta is an under-graduate in Electrical and Electronic Engineering, Ajay Kumar Garg Engineering College, Ghaziabad, 201009 India (email: shubhamgupta3121@gmail.com).
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

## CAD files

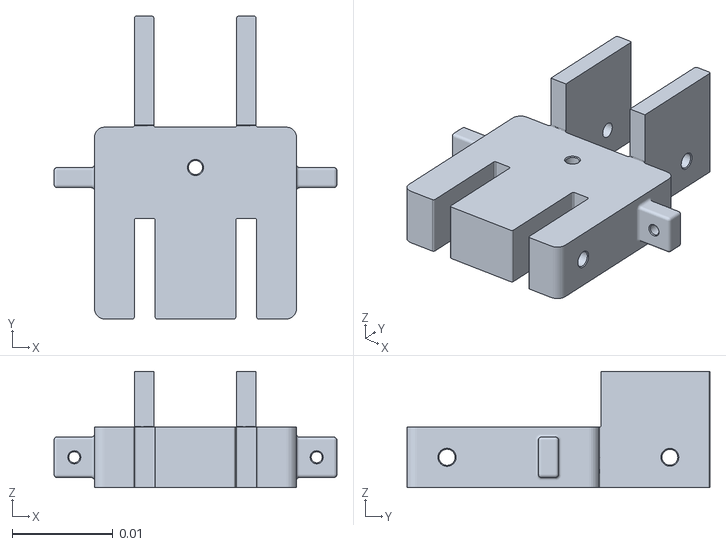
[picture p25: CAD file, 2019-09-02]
cad_files/Part1.6.stl
0.028 x 0.03 x 0.0115

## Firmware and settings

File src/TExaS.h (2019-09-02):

// TExaS.h
// Runs on LM4F120/TM4C123
// Periodic timer Timer5A which will interact with debugger and grade the lab 
// It initializes on reset and runs whenever interrupts are enabled
// Jonathan Valvano
// December 28, 2014

/* This example accompanies the book
   "Embedded Systems: Introduction to ARM Cortex M Microcontrollers"
   ISBN: 978-1469998749, Jonathan Valvano, copyright (c) 2014

 Copyright 2015 by Jonathan W. Valvano, valvano@mail.utexas.edu
    You may use, edit, run or distribute this file
    as long as the above copyright notice remains
 THIS SOFTWARE IS PROVIDED "AS IS".  NO WARRANTIES, WHETHER EXPRESS, IMPLIED
 OR STATUTORY, INCLUDING, BUT NOT LIMITED TO, IMPLIED WARRANTIES OF
 MERCHANTABILITY AND FITNESS FOR A PARTICULAR PURPOSE APPLY TO THIS SOFTWARE.
 VALVANO SHALL NOT, IN ANY CIRCUMSTANCES, BE LIABLE FOR SPECIAL, INCIDENTAL,
 OR CONSEQUENTIAL DAMAGES, FOR ANY REASON WHATSOEVER.
 For more information about my classes, my research, and my books, see
 http://users.ece.utexas.edu/~valvano/
 */

// IMPORTANT: These enumerated types are specific to Lab 8.
enum InputPorts{
  SW_PIN_PA2 = 0,
  SW_PIN_PB0 = 1,
  SW_PIN_PE0 = 4
};

enum OutputPorts{
  LED_PIN_PA3 = 0,
  LED_PIN_PB1 = 1,
  LED_PIN_PE1 = 4
};

// ************TExaS_Init*****************
// Initialize grader, triggered by timer 5A
// This needs to be called once 
// Inputs: iport input(s) connected to this port
//         oport output(s) connected to this port
// Outputs: none
void TExaS_Init(enum InputPorts iport, enum OutputPorts oport);

// ************TExaS_Stop*****************
// Stop the transfer 
// Inputs:  none
// Outputs: none
void TExaS_Stop(void);
